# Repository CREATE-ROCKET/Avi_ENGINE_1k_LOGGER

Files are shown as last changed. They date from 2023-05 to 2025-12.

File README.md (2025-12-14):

# GSE電装 ロガー

# ファイル構成
CAD: Eagle,KiCadファイル
analysis: ログ解析プログラム
src: 基板書き込みプログラム

# アナログ回路の詳細

## 推力測定

1つのセンサーに対応

[使用するロードセル](https://www.te.com/usa-en/product-FC2311-0000-0250-L.html)

センサー出力 → 作動増幅回路 (ゲイン:47) → ローパスフィルタ (500Hz, R = 3.3 kΩ, C = 0.1 μF) → ADC

## 圧力測定

4つのセンサーに対応

[使用するセンサー](https://www.bdsensors.de/fileadmin/user_upload/Download/Datenblaetter_datasheets/DB_DMK331P_E.pdf)

センサー出力 → 分圧回路 (ゲイン: 0.5) → ボルテージフォロワ → ローパスフィルタ (500Hz, R = 3.3 kΩ, C = 0.1 μF) → ADC

## 圧力測定 (以前使っていたもの、参考)

[DMK331Pのリンク](https://www.bdsensors.de/fileadmin/user_upload/Download/Datenblaetter_datasheets/DB_DMK331P_E.pdf)

本機は1つの測定用回路を搭載、**ただしこの回路は電源電圧が不足しており、上のPU5402用の回路で運用する**

電源電圧は12V, センサー出力は0-10V で運用

センサー出力 → 分圧回路 (ゲイン: 0.5) → ボルテージフォロワ → ローパスフィルタ (500Hz, R = 3.3 kΩ, C = 0.1 μF) → ADC

## 圧力測定 (より以前使っていたもの、参考)

[FSV-010MPのリンク](https://www.sayama.com/products/index.php/item?id=3137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)

本機は非搭載

電源電圧は12V, センサー出力は0-5V で運用

センサー出力 → ローパスフィルタ (500Hz, R = 3.3 kΩ, C = 0.1 μF) → ADC

## 温度測定

熱電対により測定、高温用が2つ、低温用が3つ

[使用するセンサー](https://akizukidenshi.com/catalog/g/gP-10160/)

| 温度(℃) | 温度(K) | 抵抗値(Ω) |
|---|---|---|
| 0 | 273.15  | 2.87E+04  |
| 30 | 303.15  | 8.27E+03  |
| 60 | 333.15  | 2.98E+03  |
| 90 | 363.15  | 1.27E+03  |

高温用の分圧抵抗は10kΩ、低温用の分圧抵抗は1kΩ 

## ADC
[MCP3208-BI/SL](https://www.digikey.jp/en/products/detail/microchip-technology/MCP3208-BI-SL/319444)を使用

# 解析プログラム

`analysis/analysis.py` が解析プログラム。`analysis/analysis.py`が存在するディレクトリにて `python analysis.py <inputfile.csv> <outputfile.csv>`を実行。

colabなどのnotebookで実行できるようにした「燃焼実験ログをグラフに.ipynb」も同梱しました（宮田）

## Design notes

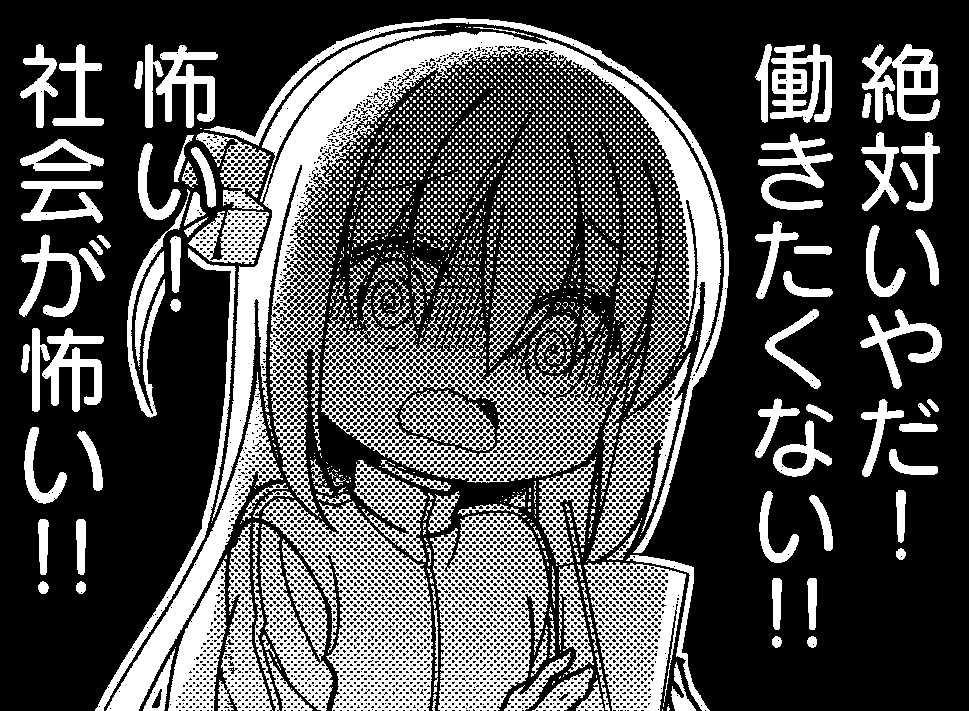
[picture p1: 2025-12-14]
CAD/bocchi.bmp

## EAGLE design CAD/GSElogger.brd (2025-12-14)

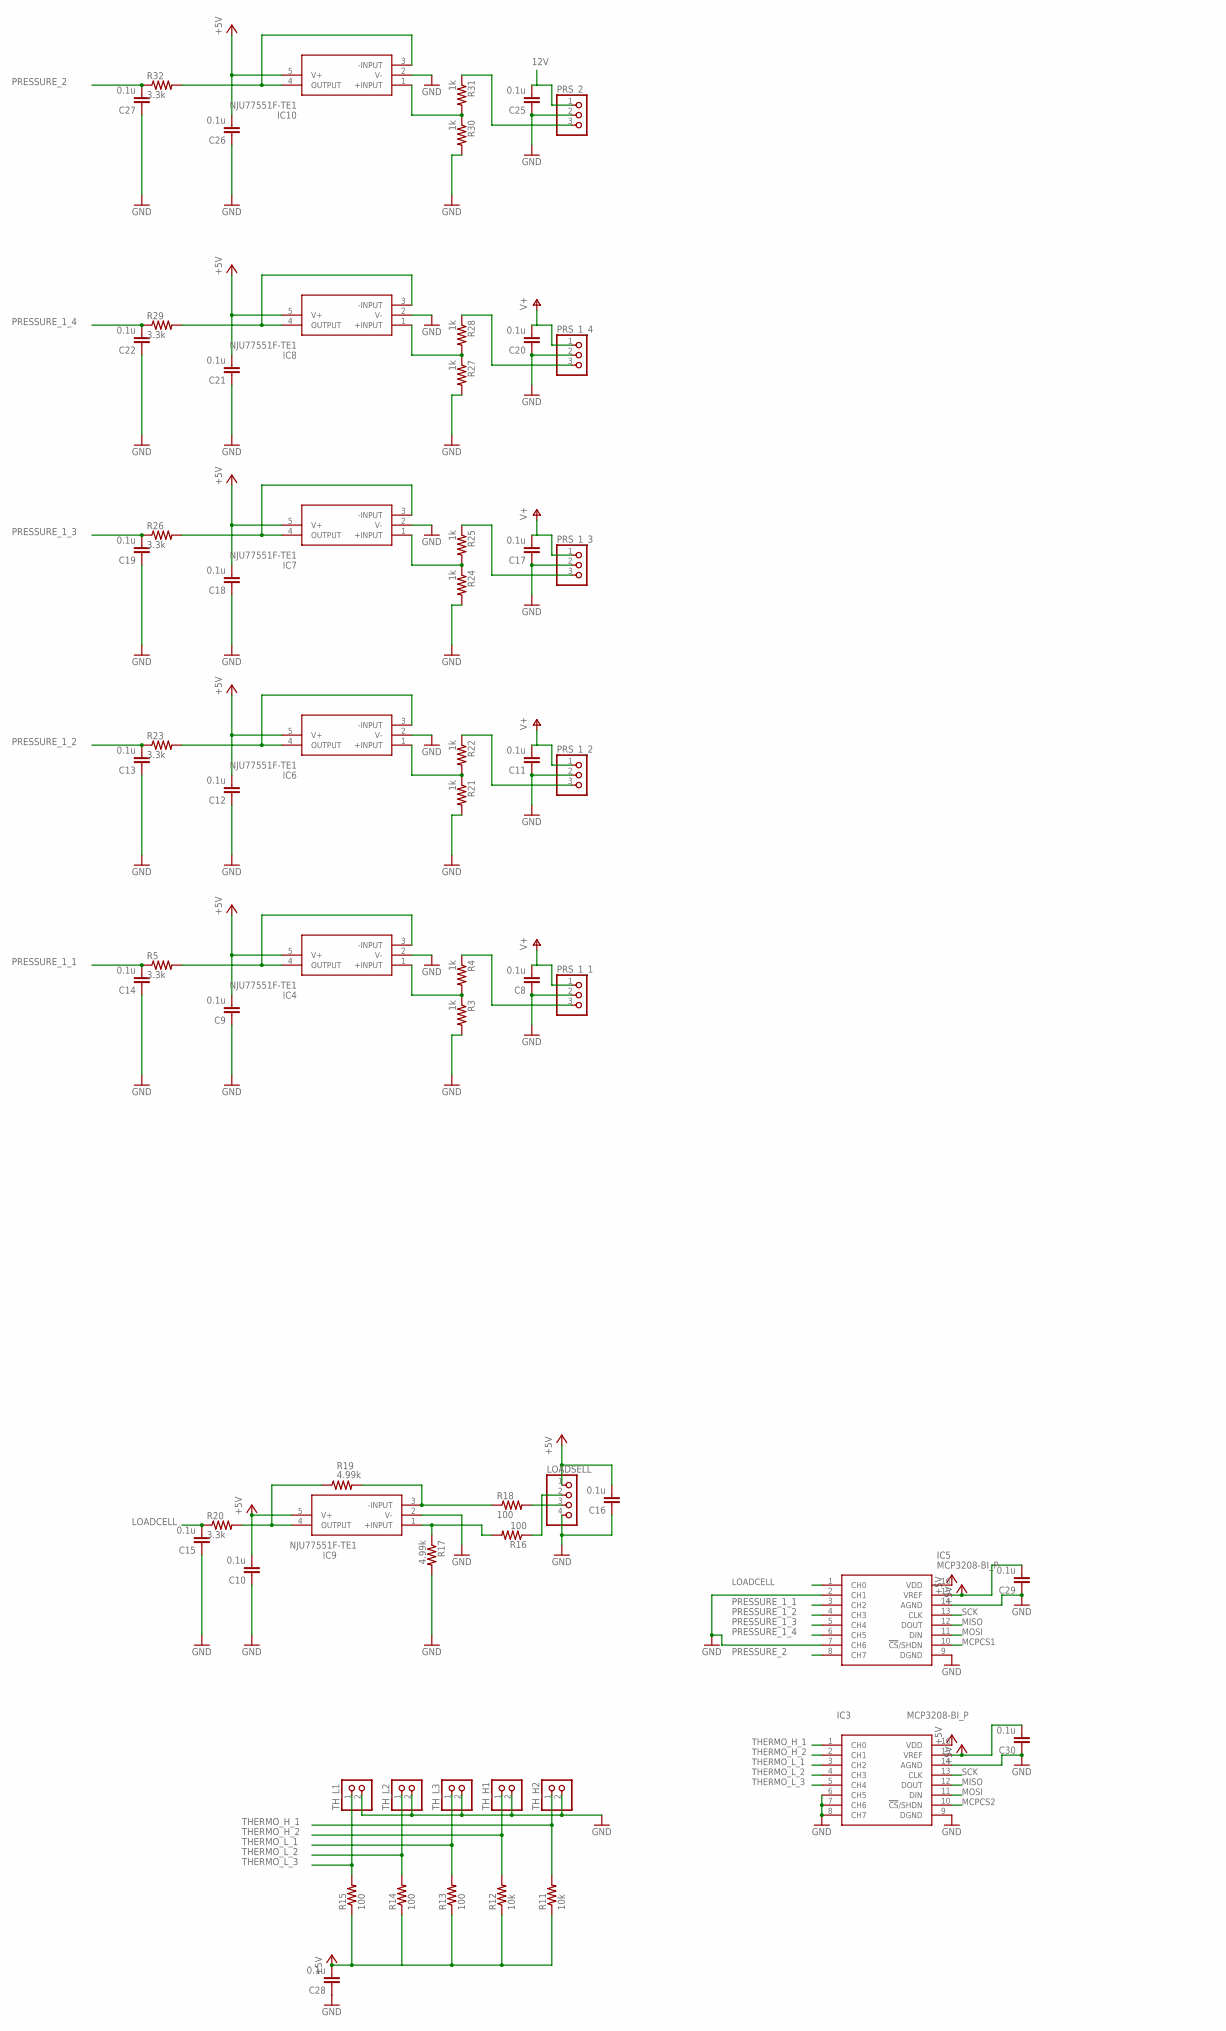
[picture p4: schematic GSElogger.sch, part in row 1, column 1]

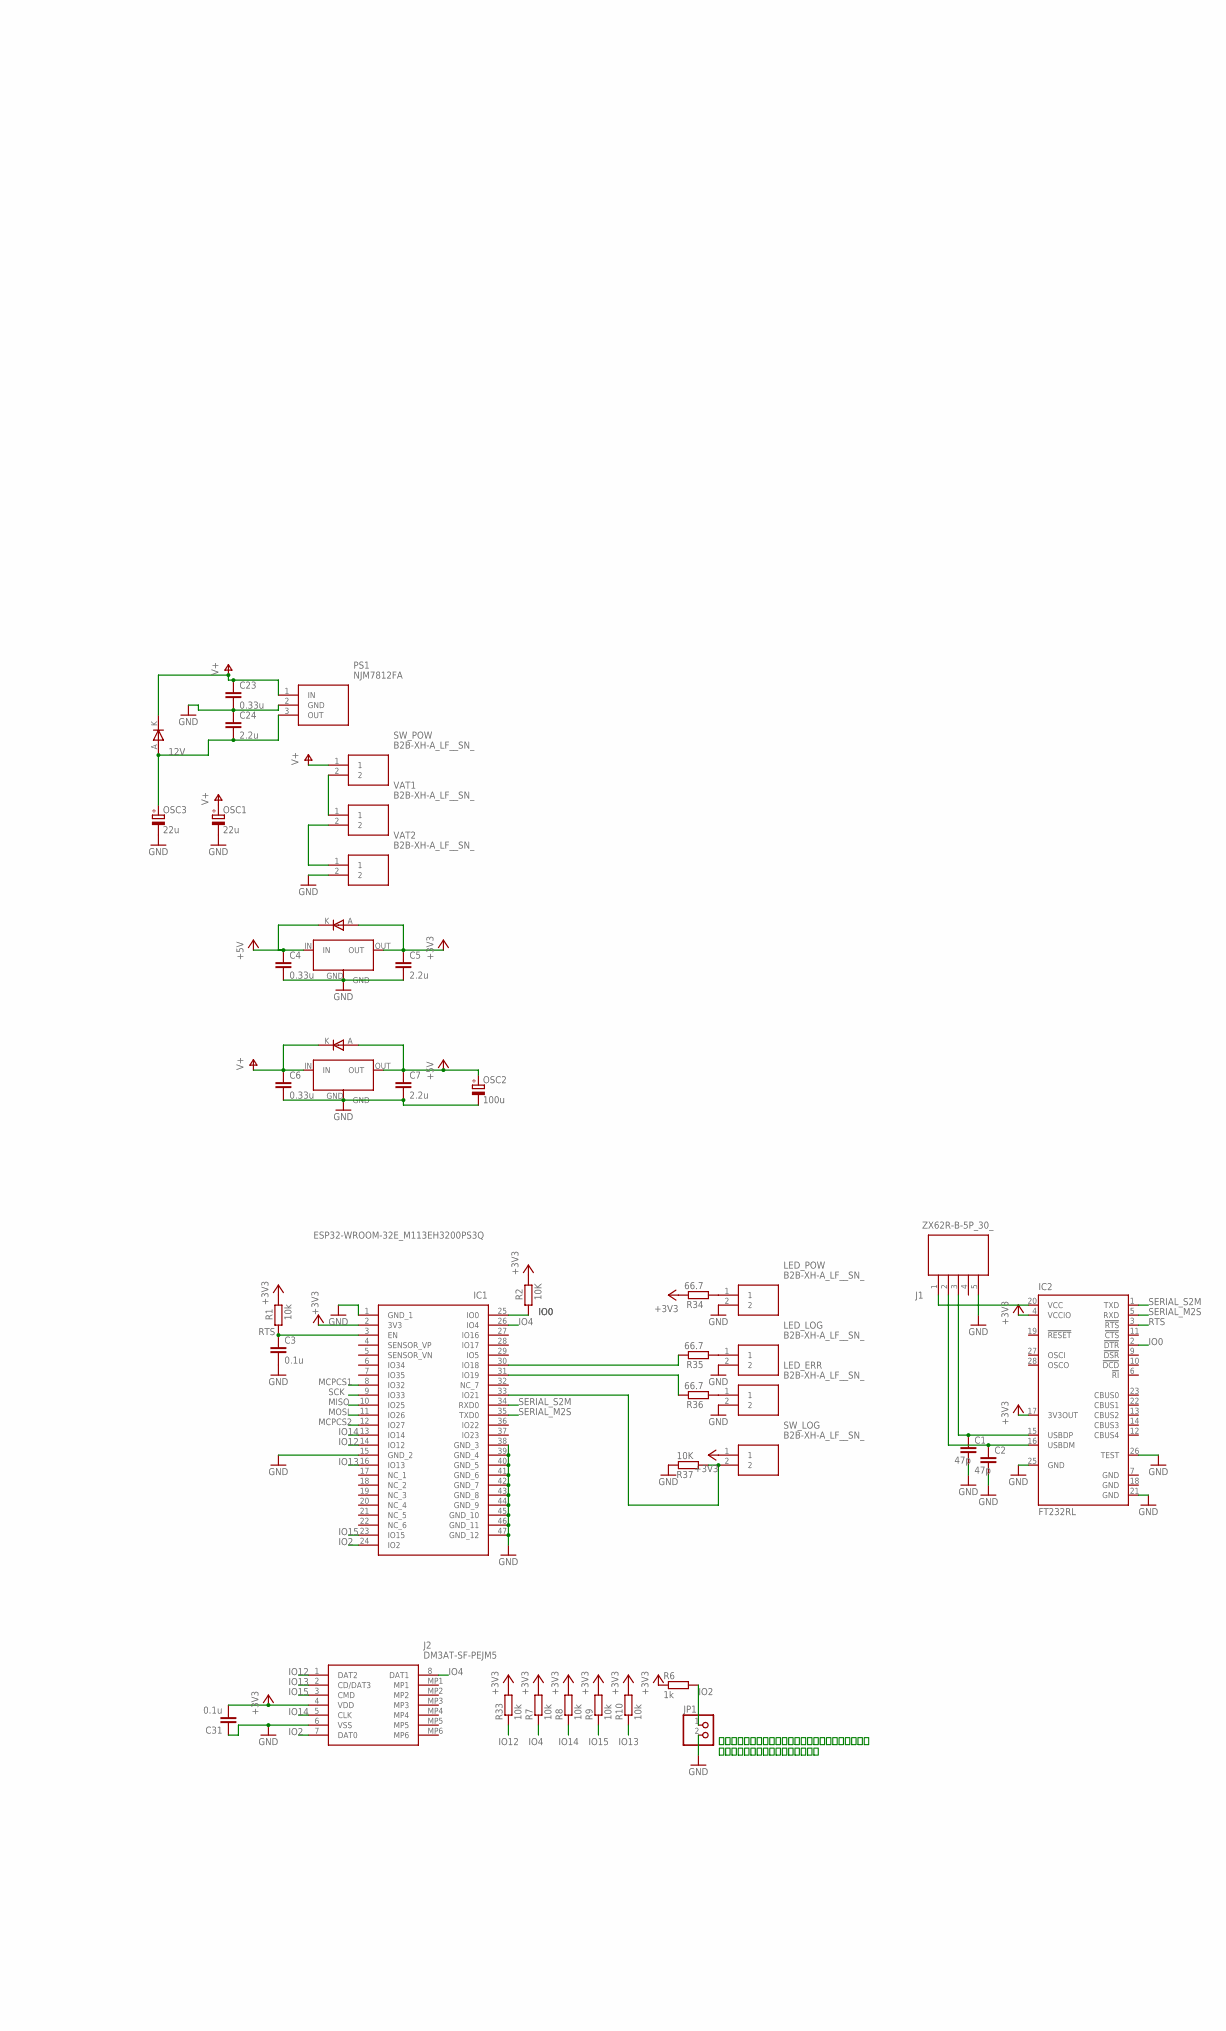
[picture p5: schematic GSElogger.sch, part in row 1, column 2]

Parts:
C1, C2: 47p; C0603
C3, C8, C9, C10, C11, C12, C13, C14, C15, C16, C17, C18, C19, C20, C21, C22, C25, C26, C27, C28, C29, C30, C31: 0.1u; C0603
C4, C6, C23: 0.33u; C0603
C5, C7, C24: 2.2u; C0603
IC1: ESP32-WROOM-32E_M113EH3200PS3Q; ESP32WROOM32EM113EH3200PS3Q0
IC2: FT232RL; SSOP28
IC3, IC5: MCP3208-BI_P; DIP781W56P254L1918H533Q16N
IC4, IC6, IC7, IC8, IC9, IC10: NJU77551F-TE1; SOT95P280X130-5N
J1: ZX62R-B-5P_30_; ZX62R-B-5P(30)
J2: DM3AT-SF-PEJM5; DM3ATSFPEJM5
JP1: PINHD-1X2; 1X02
LED_ERR: B2B-XH-A_LF__SN_; SHDR2W64P0X250_1X2_740X575X700
LED_LOG: B2B-XH-A_LF__SN_; SHDR2W64P0X250_1X2_740X575X700
LED_POW: B2B-XH-A_LF__SN_; SHDR2W64P0X250_1X2_740X575X700
LOADSELL: PINHD-1X4; 1X04
NJM7805S: 5v reg; NJM2391DL1-33
OSC1, OSC3: 22u; E2,5-6E
OSC2: 100u; E2,5-6E
PRS_1_1, PRS_1_2, PRS_1_3, PRS_1_4, PRS_2: PINHD-1X3; 1X03
PS1: NJM7812FA; TO254P500X1000X2170-3P
R1, R7, R8, R9, R10, R11, R12, R33: 10k; R0603
R2, R37: 10K; R0603
R3, R4, R6, R21, R22, R24, R25, R27, R28, R30, R31: 1k; R0603
R5, R20, R23, R26, R29, R32: 3.3k; R0603
R13, R14, R15, R16, R18: 100; R0603
R17, R19: 4.99k; R0603
R34, R35, R36: 66.7; R0603
SW_LOG: B2B-XH-A_LF__SN_; SHDR2W64P0X250_1X2_740X575X700
SW_POW: B2B-XH-A_LF__SN_; SHDR2W64P0X250_1X2_740X575X700
TH_H1, TH_H2: PINHD-1X2; 1X02
TH_L1, TH_L2, TH_L3: PINHD-1X2; 1X02
U$1, U$3, U$4: SS2040FL
U$2: 3v3 reg; NJM2391DL1-33
VAT1, VAT2: B2B-XH-A_LF__SN_; SHDR2W64P0X250_1X2_740X575X700

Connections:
12V: C24.2, C25.2, OSC3.+, PRS_2.1, PS1.3 (OUT), U$4.A
+3V3: C5.1, C31.2, IC1.2 (3V3), IC2.4 (VCCIO), IC2.17 (3V3OUT), J2.4 (VDD), R1.2, R2.2, R6.1, R7.2, R8.2, R9.2, R10.2, R33.2, R34.2, SW_LOG.1, U$1.A, U$2.OUT
+5V: C4.1, C7.1, C9.2, C10.2, C12.2, C16.2, C18.2, C21.2, C26.2, C28.2, C29.2, C30.2, IC3.15 (VREF), IC3.16 (VDD), IC4.5 (V+), IC5.15 (VREF), IC5.16 (VDD), IC6.5 (V+), IC7.5 (V+), IC8.5 (V+), IC9.5 (V+), IC10.5 (V+), LOADSELL.1, NJM7805S.OUT, OSC2.+, R11.1, R12.1, R13.1, R14.1, R15.1, U$1.K, U$2.IN, U$3.A
GND: C1.2, C2.2, C3.2, C4.2, C5.2, C6.2, C7.2, C8.1, C9.1, C10.1, C11.1, C12.1, C13.1, C14.1, C15.1, C16.1, C17.1, C18.1, C19.1, C20.1, C21.1, C22.1, C23.2, C24.1, C25.1, C26.1, C27.1, C28.1, C29.1, C30.1, C31.1, IC1.1 (GND_1), IC1.15 (GND_2), IC1.38 (GND_3), IC1.39 (GND_4), IC1.40 (GND_5), IC1.41 (GND_6), IC1.42 (GND_7), IC1.43 (GND_8), IC1.44 (GND_9), IC1.45 (GND_10), IC1.46 (GND_11), IC1.47 (GND_12), IC2.7 (GND), IC2.18 (GND), IC2.21 (GND), IC2.25 (GND), IC2.26 (TEST), IC3.6 (CH5), IC3.7 (CH6), IC3.8 (CH7), IC3.9 (DGND), IC3.14 (AGND), IC4.2 (V-), IC5.2 (CH1), IC5.7 (CH6), IC5.9 (DGND), IC5.14 (AGND), IC6.2 (V-), IC7.2 (V-), IC8.2 (V-), IC9.2 (V-), IC10.2 (V-), J1.5, J2.6 (VSS), JP1.2, LED_ERR.2, LED_LOG.2, LED_POW.2, LOADSELL.4, NJM7805S.GND, OSC1.-, OSC2.-, OSC3.-, PRS_1_1.2, PRS_1_2.2, PRS_1_3.2, PRS_1_4.2, PRS_2.2, PS1.2 (GND), R3.2, R17.2, R21.2, R24.2, R27.2, R30.2, R37.2, TH_H1.2, TH_H2.2, TH_L1.2, TH_L2.2, TH_L3.2, U$2.GND, VAT2.2
IO0: IC1.25 (IO0), IC2.2 (!DTR), R2.1
IO2: IC1.24 (IO2), J2.7 (DAT0), JP1.1, R6.2
IO4: IC1.26 (IO4), J2.8 (DAT1), R7.1
IO12: IC1.14 (IO12), J2.1 (DAT2), R33.1
IO13: IC1.16 (IO13), J2.2 (CD/DAT3), R10.1
IO14: IC1.13 (IO14), J2.5 (CLK), R8.1
IO15: IC1.23 (IO15), J2.3 (CMD), R9.1
LOADCELL: C15.2, IC5.1 (CH0), R20.1
MCPCS1: IC1.8 (IO32), IC5.10 (!CS!/SHDN)
MCPCS2: IC1.12 (IO27), IC3.10 (!CS!/SHDN)
MISO: IC1.10 (IO25), IC3.12 (DOUT), IC5.12 (DOUT)
MOSI: IC1.11 (IO26), IC3.11 (DIN), IC5.11 (DIN)
unnamed: IC4.3 (-INPUT), IC4.4 (OUTPUT), R5.2
unnamed: IC2.20 (VCC), J1.1
unnamed: C2.1, IC2.16 (USBDM), J1.2
unnamed: C1.1, IC2.15 (USBDP), J1.3
unnamed: IC4.1 (+INPUT), R3.1, R4.2
unnamed: IC6.1 (+INPUT), R21.1, R22.2
unnamed: PRS_1_1.3, R4.1
unnamed: PRS_1_2.3, R22.1
unnamed: IC6.3 (-INPUT), IC6.4 (OUTPUT), R23.2
unnamed: IC7.1 (+INPUT), R24.1, R25.2
unnamed: PRS_1_3.3, R25.1
unnamed: IC7.3 (-INPUT), IC7.4 (OUTPUT), R26.2
unnamed: IC8.1 (+INPUT), R27.1, R28.2
unnamed: PRS_1_4.3, R28.1
unnamed: IC8.3 (-INPUT), IC8.4 (OUTPUT), R29.2
unnamed: IC9.4 (OUTPUT), R19.1, R20.2
unnamed: VAT1.2, VAT2.1
unnamed: IC10.1 (+INPUT), R30.1, R31.2
unnamed: PRS_2.3, R31.1
unnamed: IC10.3 (-INPUT), IC10.4 (OUTPUT), R32.2
unnamed: SW_POW.2, VAT1.1
unnamed: LOADSELL.2, R16.1
unnamed: LED_POW.1, R34.1
unnamed: IC9.3 (-INPUT), R18.1, R19.2
unnamed: LOADSELL.3, R18.2
unnamed: LED_LOG.1, R35.1
unnamed: LED_ERR.1, R36.1
unnamed: IC9.1 (+INPUT), R16.2, R17.1
unnamed: IC1.30 (IO18), R35.2
unnamed: IC1.31 (IO19), R36.2
unnamed: IC1.33 (IO21), R37.1, SW_LOG.2
PRESSURE_1_1: C14.2, IC5.3 (CH2), R5.1
PRESSURE_1_2: C13.2, IC5.4 (CH3), R23.1
PRESSURE_1_3: C19.2, IC5.5 (CH4), R26.1
PRESSURE_1_4: C22.2, IC5.6 (CH5), R29.1
PRESSURE_2: C27.2, IC5.8 (CH7), R32.1
RTS: C3.1, IC1.3 (EN), IC2.3 (!RTS), R1.1
SCK: IC1.9 (IO33), IC3.13 (CLK), IC5.13 (CLK)
SERIAL_M2S: IC1.35 (TXD0), IC2.5 (RXD)
SERIAL_S2M: IC1.34 (RXD0), IC2.1 (TXD)
THERMO_H_1: IC3.1 (CH0), R11.2, TH_H2.1
THERMO_H_2: IC3.2 (CH1), R12.2, TH_H1.1
THERMO_L_1: IC3.3 (CH2), R13.2, TH_L3.1
THERMO_L_2: IC3.4 (CH3), R14.2, TH_L2.1
THERMO_L_3: IC3.5 (CH4), R15.2, TH_L1.1
V+: C6.1, C8.2, C11.2, C17.2, C20.2, C23.1, NJM7805S.IN, OSC1.+, PRS_1_1.1, PRS_1_2.1, PRS_1_3.1, PRS_1_4.1, PS1.1 (IN), SW_POW.1, U$3.K, U$4.K

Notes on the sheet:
書き込み時はこのピンヘッダを導通させてください。 それ以外の時は開放してください。

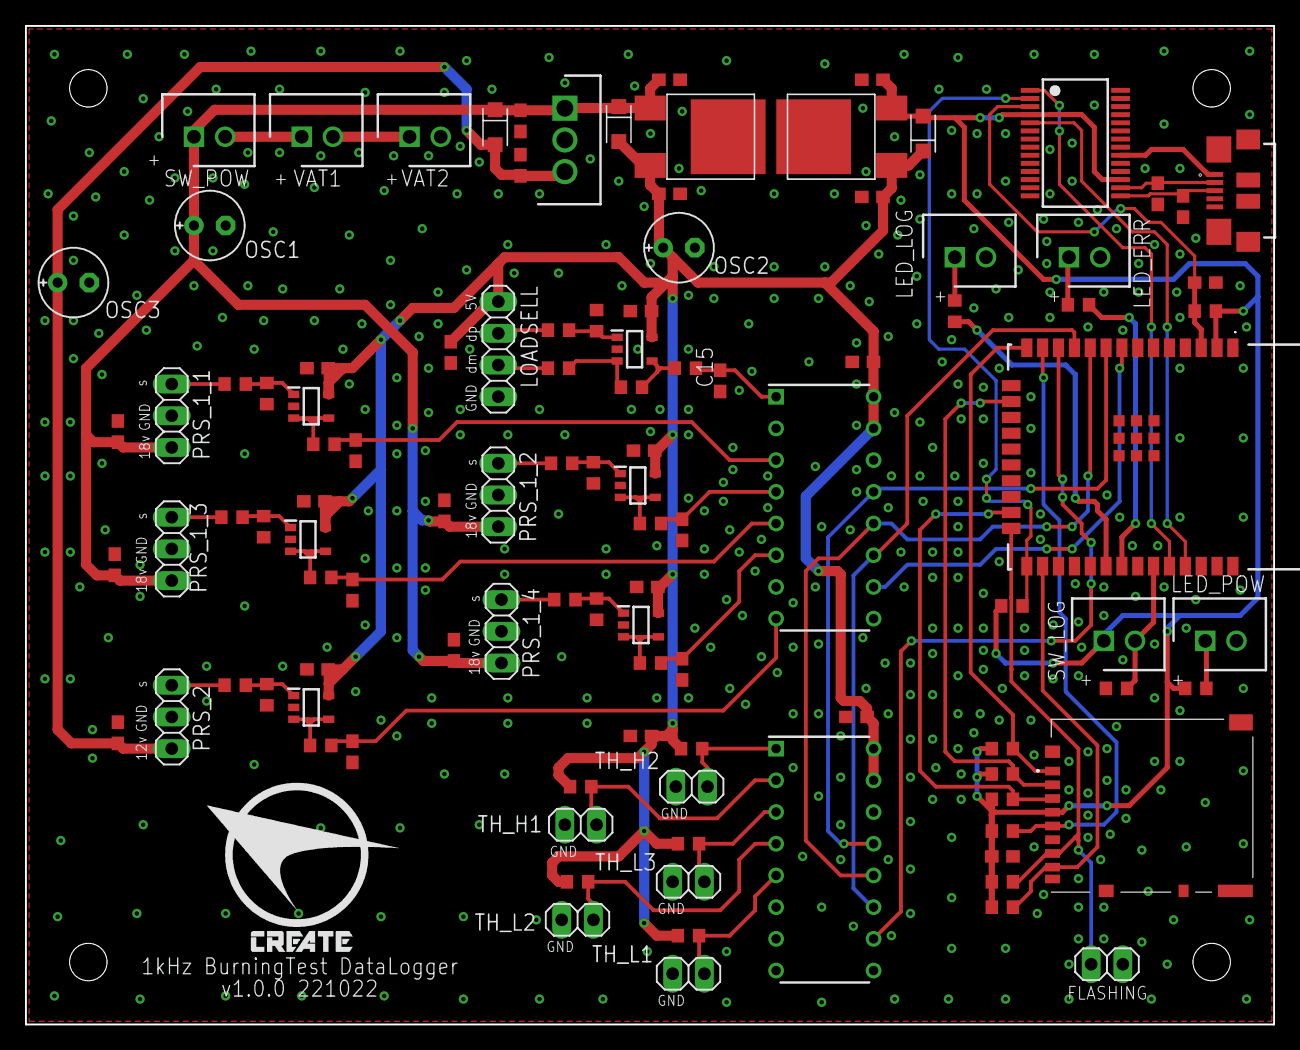
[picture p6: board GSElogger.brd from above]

Board: 2 copper layers, 100.0 x 80.0 mm, 108 parts (0 on the bottom side), 62 nets.

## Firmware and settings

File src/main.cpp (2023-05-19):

#include <Arduino.h>
#include <SPICREATE.h>
#include <mcp3208.h>
#include <SDIOLogWrapper.hpp>
#include <SDIOLogWrapper.hpp>

#define SCK1 33
#define MISO1 25
#define MOSI1 26
#define MCPCS1 32
#define MCPCS2 27
#define LED_ERR 19
#define VALVE_BRD_STAT 18
#define LOGGINGINTERVAL 1

#define QUEUESTRINGSIZE 128

SPICREATE::SPICreate SPIC1;
MCP mcp3208_0;
MCP mcp3208_1;

xTaskHandle xlogHandle;
uint8_t isLoggintGoing = 0;

IRAM_ATTR void logging(void *parameters)
{
  portTickType xLastWakeTime = xTaskGetTickCount();
  for (;;)
  {
    uint16_t adcData[16];
    char *bfChar = new char[QUEUESTRINGSIZE];
    if (bfChar != NULL)
    {
      bfChar[0] = '\0';
      uint8_t xQueueWaitCount = SDIOLogWrapper::countWaitingQueue();

      uint32_t startTime = micros();

      for (int i = 0; i < 8; i++)
      {
        adcData[i] = mcp3208_0.Get(i);
        adcData[8 + i] = mcp3208_1.Get(i);
      }

      uint32_t stopTime = micros();

      sprintf(bfChar, "%d,%d,%d,", xQueueWaitCount, startTime, stopTime);
      for (int i = 0; i < 16; i++)
      {
        sprintf(bfChar, "%s%d,", bfChar, adcData[i]);
      }
      sprintf(bfChar, "%s%d\n", bfChar, digitalRead(VALVE_BRD_STAT));

      if (SDIOLogWrapper::appendQueue(bfChar) == 1)
      {
        Serial.println("queue filled!");
      }
    }

    vTaskDelayUntil(&xLastWakeTime, LOGGINGINTERVAL / portTICK_PERIOD_MS);
  }
}

void setup()
{
  // io init
  Serial.begin(115200);
  pinMode(LED_ERR, OUTPUT);
  pinMode(21, INPUT_PULLDOWN);
  pinMode(VALVE_BRD_STAT,INPUT_PULLUP);
  digitalWrite(LED_ERR, HIGH);
  SPIC1.begin(VSPI, SCK1, MISO1, MOSI1);
  mcp3208_0.begin(&SPIC1, MCPCS1, 6000000);
  mcp3208_1.begin(&SPIC1, MCPCS2, 6000000);
}

void loop()
{
  // put your main code here, to run repeatedly:

  if ((digitalRead(21) == HIGH) && (isLoggintGoing == 0))
  {
    digitalWrite(LED_ERR, LOW);
    isLoggintGoing = 1;
    SDIOLogWrapper::makeQueue(128);
    SDIOLogWrapper::setSaveFileName("/aiueo.csv");
    SDIOLogWrapper::setSaveInterval(100);

    Serial.printf("SD init result: %d\n", SDIOLogWrapper::initSD());
    SDIOLogWrapper::openFile();
    SDIOLogWrapper::writeTaskCreate(APP_CPU_NUM);
    xTaskCreateUniversal(logging, "logging", 8192, NULL, configMAX_PRIORITIES, &xlogHandle, PRO_CPU_NUM);
  }

  delay(1000);

  if ((digitalRead(21) == LOW) && (isLoggintGoing == 1))
  {
    digitalWrite(LED_ERR, HIGH);
    vTaskDelete(xlogHandle);
    delay(1000);
    SDIOLogWrapper::writeTaskDelete();
    Serial.println("logTask killed");
    SDIOLogWrapper::deleteQueue();
    SDIOLogWrapper::closeFile();
    SDIOLogWrapper::deinitSD();
    isLoggintGoing = 0;
  }
  delay(1000);
}

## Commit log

2022-02-13 [add] mcp3208 library and unstable 1k logging
    [main.cpp]
2022-05-18 [fix] stabilized sd 1k logging
    [main.cpp]
2022-05-28 [add] SDIOLogWrapper but RTOS task fails compiling
    [main.cpp]
2022-08-23 ⚡️ ファイル名変更の関数を追加、ネームスペース化
2022-08-25 ✅ newとdeleteを使用したqueueの使用領域の削減の実装
2022-09-03 📝 add README.md
2022-11-01 🚑️ newに失敗したときの処理の追加、およびロギング始/終時にQueueを作成/削除するよう変更
2022-11-08 ✅Queueが埋まった際リブートしないよう変更、放置テスト通過
2022-11-21 ✨ 外部スイッチによるロギング開始・停止を実装
2023-03-07 add led err indicator
2023-04-07 ロードセル荷重試験による推力算出方法の変更
2023-04-11 新サーミスタに合わせプログラムを変更
2023-05-18 低温用・高温用サーミスタの数を実運用に合わせて変更
2023-05-19 バルブ基板からのH/L信号を記録する機能を追加
2023-05-19 温度計算を修正、バルブ基板の情報を解析に反映
2023-05-26 tqdmが必要ないようにコードを変更
2023-05-26 解析プログラムの実行方法を追加
2023-06-25 Update README Document
    [thermistor_TvsR.xlsx]
2025-08-28 add notebook analysis file
    ジュピターノートブックなどでログの簡単なグラフが見えるファイルを作りました
2025-08-28 コメント、説明文を修正
2025-11-22 analysis.pyを新ロードセル対応版に修正
    遅くなってすいません。
    notebookだけでなくanalysis.pyも修正しました
